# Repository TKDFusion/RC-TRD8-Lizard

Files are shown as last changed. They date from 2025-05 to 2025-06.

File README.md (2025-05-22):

Lizard is a 3D printed RC race car for onroad usage. The full description of this project is available on Instructables: https://www.instructables.com/Lizard-3D-Printed-RC-Race-Car/

Here, you can find the Gerber files for the PCBs and the sketches required for the ESP32 microcontroller in the remote control and in the car. Also, you can find the codes required to operate a separate data logger alongside the car, including MATLAB functions to evaluate the recorded data graphically. Further, all files for printing are provided as .stl and .stp files.

Also, I added the BOM as an Excel file, and you can find .stp files of the different part groups as well as of the full car assembly, as an aid in assembling the car.

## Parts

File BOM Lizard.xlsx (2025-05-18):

Group | Part | Content | Quantity | Description/comment | Source/Link | Price per unit | Total | Sum
Actuators | Cytron MD 20A | 1 | 1 | 20 A brushed DC motor driver | https://eu.robotshop.com/de/products/cytron-20a-6-30v-dc-motorsteuerung | 23.80 € | 23.80 € | 954.12 €
Actuators | 775 12 V 10k rpm 150 W | 1 | 1 | 775 brushed DC motor | https://www.amazon.de/dp/B07BGWMYYM | 13.99 € | 13.99 €
Actuators | 40-45mm motor cooler | 1 | 1 | Cooling block for DC motor | https://www.ebay.de/itm/224586911069 | 15.95 € | 15.95 €
Actuators | Claw clutch (5 mm shaft coupler) | 1 | 1 | shaft adapter for 775 motor | https://www.amazon.de/dp/B09MLV2G45/ | 10.99 € | 10.99 €
Actuators | Servo motor | 1 | 1 | Graupner DES 708 BB MG | https://www.derkum-modellbau.com/rc-_-elektronik/servos/servos/graupner-des-708-bb-mg-digital-servo | 43.90 € | 43.90 €
Actuators | Servo saver | 1 | 1 | Tamiya high torque servo saver | https://tamico.de/Tamiya-Servo-Saver-Hi-Torque-weiss-50473 | 13.39 € | 13.39 €
Wheels | Carson 1:8 buggy | 2 | 2 | Carson buggy wheels | https://www.amazon.de/Carson-500900075-Felgen-Set-Modellbauzubeh%C3%B6r-schwarz/dp/B003MX6LOG/ | 11.99 € | 23.98 €
Batteries | SLS XTRON 5000MAH 3S1P | 1 | 1 | car battery | https://www.stefansliposhop.de/akkus/sls-xtron/sls-xtron-20c/sls-xtron-5000mah-3s1p-11-1v-20c-40c::985.html | 51.90 € | 51.90 €
Batteries | Duracell NiMH AA 2500 mAh | 4 | 2 | RC batteries | https://www.reichelt.de/nimh-akku-aa-mignon-2500-mah-4er-pack-dura-nimh-aa4-p357195.html | 12.95 € | 25.90 €
Bearings | 683ZZ | 20 | 2 | 3x7x3 | https://www.amazon.de/sourcing-map-Rillenkugellager-Doppelschild-Kohlenstoffstahl/dp/B07H5HXND9/ | 9.49 € | 18.98 €
Bearings | 6802ZZ | 10 | 2 | 15x24x5 | https://www.amazon.de/XiKe-Kugellager-15x24x5mm-Abgedichtet-Rillenkugellager/dp/B09SD74PZV/ | 11.59 € | 23.18 €
Bearings | 6804ZZ | 10 | 1 | 20x32x7 | https://www.amazon.de/XiKe-Kugellager-20x32x7mm-Abgedichtet-Rillenkugellager/dp/B09SD8RKJT/ | 12.99 € | 12.99 €
Bearings | 608ZZ | 20 | 1 | 8x22x7 | https://www.amazon.de/HonLena-Kugellager-Shielded-Rillenkugellager-Skateboard/dp/B08K936Y1Z/ | 9.99 € | 9.99 €
Bearings | 605ZZ | 10 | 1 | 5x14x5 | https://www.amazon.de/sourcing-map-Rillenkugellager-5mmx14mmx5mm-Kohlenstoffstahl/dp/B07H936D3C/ | 7.99 € | 7.99 €
Bearings | MR85ZZ | 10 | 1 | 5x8x2.5 | https://www.amazon.de/dp/B07CKN7NPK | 8.14 € | 8.14 €
Bearings | 0303 sleeve bearing | 50 | 1 | 3x4.5x3 | https://www.amazon.de/dp/B06Y6D951G | 8.63 € | 8.63 €
Bearings | 0306 sleeve bearing | 50 | 1 | 3x4.5x6 | https://www.amazon.de/dp/B06Y617JGS | 9.66 € | 9.66 €
Connectors | Molex 16-02-0102 | 100 | 1 | Molex SL female crimp pin | https://www.mouser.de/ProductDetail/Molex/16-02-0102?qs=UAyrm%2FnZ%252BCifWkt7bqgfPw%3D%3D | 8.50 € | 8.50 €
Connectors | Molex 70543-0001 | 10 | 1 | Molex SL 2-pin socket | https://www.mouser.de/ProductDetail/Molex/70543-0001?qs=tYx%252BZc2nXqpCsE0XoulATg%3D%3D | 7.60 € | 7.60 €
Connectors | Molex 70543-0002 | 10 | 1 | Molex SL 3-pin socket | https://www.mouser.de/ProductDetail/Molex/70543-0002?qs=tYx%252BZc2nXqrtKxtMAO73sw%3D%3D | 7.67 € | 7.67 €
Connectors | Molex 70543-0003 | 10 | 1 | Molex SL 4-pin socket | https://www.mouser.de/ProductDetail/Molex/70543-0003?qs=tYx%252BZc2nXqp%2Fu7bSTX42XQ%3D%3D | 8.59 € | 8.59 €
Connectors | Molex 50-57-9402 | 10 | 1 | Molex SL 2-pin female connector | https://www.mouser.de/ProductDetail/Molex/50-57-9402?qs=u6Gr9%2FNt%252B%2F9jh%2FRowNBxRQ%3D%3D | 2.53 € | 2.53 €
Connectors | Molex 50-57-9403 | 10 | 1 | Molex SL 3-pin female connector | https://www.mouser.de/ProductDetail/Molex/50-57-9403?qs=u6Gr9%2FNt%252B%2F9Ok3bHhq8UPA%3D%3D | 1.71 € | 1.71 €
Connectors | Molex 50-57-9404 | 10 | 1 | Molex SL 4-pin female connector | https://www.mouser.de/ProductDetail/Molex/50-57-9404?qs=u6Gr9%2FNt%252B%2F%2FUw3Dr7T8xxg%3D%3D | 2.17 € | 2.17 €
Connectors | Jamara XT60 | 1 | 1 | M/F pair of high-current connectors | https://www.reichelt.de/steckverbinder-fuer-li-polymer-akkus-2-polig-xt60-hstxt60-stbu-p207648.html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 | 1.99 € | 1.99 €
Electronics | ESP32 MCU | 2 | 1 | with connector for external antenna | https://www.amazon.de/iHaospace-ESP32-WROOM-32U-ESP32-DevKitC-Development-Entwicklungsboard/dp/B0CT3BHJ4C/ | 15.99 € | 15.99 €
Electronics | Antenna | 2 | 1 | external antenna for ESP32 | https://www.amazon.de/2-4GHz-Omnidirektionale-Antenne-802-11n-Pigtail/dp/B07FDN82D8/ | 6.99 € | 6.99 €
Electronics | ADS1115 | 1 | 2 | ADC boards | https://www.amazon.de/AZDelivery-ADS1115-Kanäle-Arduino-Raspberry/dp/B07QHWLTTS/ | 5.99 € | 11.98 €
Electronics | Marquardt 01801.1148-02 | 1 | 2 | Marquardt on-off switch, series 1801 | https://www.reichelt.de/de/de/shop/produkt/wippschalter_ein_-_aus_1_polig_schwarz-257132 | 1.60 € | 3.20 €
Electronics | ONPOW anti-vandal push button | 1 | 4 | with LED, 16 mm mounting hole | https://www.pollin.de/p/onpow-vandalismusgeschuetzter-taster-220-v-ac-0-5-a-1no-weiss-421220 | 4.55 € | 18.20 €
Electronics | Battery holder | 1 | 1 | 6xAA | https://funduinoshop.com/diy-werkstatt/stromversorgung/batteriefaecher-und-klemmen/batteriefach-6x-aa-9v-ohne-stecker | 1.97 € | 1.97 €
Electronics | Omeg PC20BU 10k linear | 1 | 1 | Poti with 6 mm shaft | https://www.pollin.de/p/omeg-potentiometer-pc20bu-10-ko-linear-240663 | 1.90 € | 1.90 €
Electronics | Bourns 93R1AR2215L | 1 | 2 | High-quality poti with 6 mm shaft | https://www.reichelt.de/drehpotentiometer-10-kohm-linear-6-mm-bou-93r1ar22a15l-p232657.html | 6.25 € | 12.50 €
Electronics | Sunon MF50151VX-1000U-A99 | 1 | 2 | 50x50x15 mm 12 V axial fan | https://www.reichelt.de/de/de/shop/produkt/luefter_12_vdc_50x50x15mm_serie_me-397682 | 2.99 € | 5.98 €
Electronics | 0.96" OLED display | 1 | 2 | 128x64 px, SSD1306 chip | https://www.amazon.de/AZDelivery-Display-Arduino-Raspberry-gratis/dp/B01L9GC470 | 6.62 € | 13.24 €
Electronics | NTC temp sensor | 1 | 2 | 10k, B-value 3435 | https://www.amazon.de/InLine-Temperatursensor-mit-Kabel-1m/dp/B001IQ0L2M | 8.48 € | 16.96 €
Electronics | Speed sensor | 1 | 1 | HC-020K wheel encoder | https://funduinoshop.com/elektronische-module/elektromotoren-und-zubehoer/servomotoren/hc-020k-schrittzaehler-fuer-motoren-wheel-encoder | 2.57 € | 2.57 €
Electronics | LED stripe red | 1 | 1 | 480 LEDs/m, 4 mm width, 2 m length | https://www.amazon.de/COB-LED-Fosingut-USB-Hintergrundbeleuchtung/dp/B0D3T8R8HF | 10.99 € | 10.99 €
Electronics | LED flashlight | 2 | 1 | designed for 2xAAA battery | https://www.amazon.de/flintronic-Taschenlampe-Wasserdicht-AAA-Batterien-enthalten/dp/B09MM7L6LG | 7.99 € | 7.99 €
Filament | PETG filament | 1 kg | 2 | Prusament Jet Black | https://www.prusa3d.com/product/prusament-petg-jet-black-1kg/ | 29.99 € | 59.98 €
Filament | PETG filament | 1 kg | 1 | Prusament Jungle Green | https://www.prusa3d.com/product/prusament-petg-jungle-green-1kg/ | 29.99 € | 29.99 €
Filament | TPU filament | 750 g | 1 | BASF TPU64D | https://www.galaxus.de/de/s1/product/basf-tpu64d-schwarz-175-mm-750-g-tpu-175-mm-750-g-schwarz-3d-filament-18455255 | 48.94 € | 48.94 €
Magnets | Neodymium disc magnet (south) | 1 | 4 | 8x3.5x3 | https://www.magnethandel.de/neodym-ringmagnete-senkung-sued-8-35-3-mm-schwarz | 0.31 € | 1.24 €
Magnets | Neodymium disc magnet (north) | 1 | 4 | 8x3.5x3 | https://www.magnethandel.de/neodym-ringmagnete-senkung-nord-8-35-3-mm-schwarz | 0.31 € | 1.24 €
Metal bars | Steel round bar | 1 m | 1 | 3 mm diameter (not more than 3 mm!) | local hardware store | 5.00 € | 5.00 €
Metal bars | Steel round bar | 1 m | 1 | 4 mm diameter | local hardware store | 5.00 € | 5.00 €
PCB parts | Gaptec LC78_05-2.0 | 1 | 1 | 5V 2A DC-DC converter | https://www.reichelt.de/dc-dc-wandler-6-5-30-vin-5-0-vout-2-a-sip-3-lc78-05-2-0-p242830.html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 | 13.30 € | 13.30 €
PCB parts | Traco TSR 1-2433E | 1 | 1 | 3V3 1A DC-DC converter | https://www.reichelt.de/de/de/shop/produkt/dc_dc-wandler_tsr_1e_1_a_6-36_3_3_vdc_sil-3-288646?search=2433e | 3.99 € | 3.99 €
PCB parts | Gaptec LC78_03-2.0 | 1 | 1 | 3V3 2A DC-DC converter | https://www.reichelt.de/de/de/shop/produkt/dc_dc-wandler_4_5_-_30_vin_3_3_vout_2_a_sip-3-242828 | 13.30 € | 13.30 €
PCB parts | Quadrios resistor set | 1 | 1 | 20x20 different resistors | https://www.pollin.de/p/quadrios-widerstands-set-201711p004-metallschicht-0-5-watt-1-800557 | 12.90 € | 12.90 €
PCB parts | Panasonic FC 100/50 | 1 | 2 | Radial Cap, 100 µF, 50 V, 5 mm spacing | https://www.reichelt.de/elko-radial-100-f-50-v-105-c-low-esr-10-x-12-5-mm-rm-5-0-rad-fc-100-50-p84620.html | 0.22 € | 0.44 €
PCB parts | ECC KTS500B106K (X7R) | 1 | 2 | SMD Capacitor, 10 µF, 50 V, G2220 | https://www.reichelt.de/smd-kerko-2220-10-f-50-v-10-mlcc-ecc-kts500b106k-p256486.html | 0.99 € | 1.98 €
PCB parts | X7R-G1206 22/10 | 1 | 6 | SMD Capacitor, 22 µF, 10 V, G1206 | https://www.reichelt.de/smd-vielschichtkondensator-g1206-22-f-10v-x7r-g1206-22-10-p89742.html | 0.26 € | 1.56 €
PCB parts | WAL 0805B104K500 | 1 | 3 | SMD Capacitor, 100 nF, 50 V, 0805(2012) | https://www.reichelt.de/smd-kerko-0805-100-nf-50v-10-x7r-mlcc-wal-0805b104k500-p346808.html | 0.03 € | 0.09 €
PCB parts | WAL 0805B102K500 | 1 | 1 | SMD Capacitor, 1 nF, 50 V | https://www.reichelt.de/de/de/shop/produkt/smd-kerko_0805_1_nf_50v_10_x7r_mlcc-346784 | 0.03 € | 0.03 €
PCB parts | X5R-G0805 10/16 | 1 | 1 | SMD Capacitor, 10 µF, 16 V (0805) | https://www.reichelt.de/de/de/shop/produkt/smd-vielschichtkondensator_g0805_-_10_f_16v-89734 | 0.05 € | 0.05 €
PCB parts | ACS712 ELCTR-30 | 1 | 1 | SOIC-8 current sensor | https://www.reichelt.de/de/de/shop/produkt/stromsensor_ac_dc_5_v_soic-8-237785 | 3.20 € | 3.20 €
PCB parts | IRLML 6244 | 1 | 4 | SMD MOSFET | https://www.reichelt.de/de/de/shop/produkt/mosfet_n-ch_20v_6_3a_0_021r_sot-23-132145 | 0.15 € | 0.60 €
PCB parts | WAGO 2604-3104 | 1 | 1 | PCB terminal block | https://www.reichelt.de/de/de/shop/produkt/leiterplattenklemme_-_rm_5_mm_4_mm_4-polig-195366 | 3.50 € | 3.50 €
PCB parts | 20-pin socket terminal strip | 1 | 4 | 2.54 mm spacing, height 8.5 mm | https://www.reichelt.de/20pol-buchsenleiste-gerade-rm-2-54-h-8-5mm-bl-1x20g8-2-54-p51827.html | 0.30 € | 1.20 €
PCB parts | 10-pin socket terminal strip | 1 | 2 | 2.54 mm spacing, height 8.5 mm | https://www.reichelt.de/10pol-buchsenleiste-gerade-rm-2-54-h-8-5mm-bl-1x10g8-2-54-p51826.html | 0.22 € | 0.44 €
PCB parts | IMAXX H7810 | 1 | 1 | miniOTO fuse holder | https://www.reichelt.de/kfz-sicherungshalter-minioto-30-a-125-v-printmontage-imaxx-h7810-p229120.html | 0.99 € | 0.99 €
PCB parts | IMAXX F7030 | 1 | 1 | miniOTO fuse, 30 A | https://www.reichelt.de/kfz-sicherung-minioto-30-a-gruen-imaxx-f7030-p242101.html | 0.33 € | 0.33 €
PCB parts | IRLZ 44N | 1 | 3 | n-Channel logic level MOSFET, TO-220 | https://www.reichelt.de/mosfet-n-ch-55v-47a-110w-to-220ab-irlz-44n-p129819.html | 0.70 € | 2.10 €
PCB parts | IRFP7430PBF | 1 | 1 | n-Channel power MOSFET, TO-247 | https://www.reichelt.de/mosfet-n-kanal-40-v-195-a-rds-on-0-001-ohm-to247ac-irfp7430pbf-p257333.html | 3.10 € | 3.10 €
PCB parts | 1N-5819 | 1 | 1 | Diode | https://www.reichelt.de/de/de/shop/produkt/schottkydiode_40_v_1_a_do-41-41850 | 0.05 € | 0.05 €
PCB parts | PCA9685 | 1 | 1 | TSSOP-28 IC, PWM driver | https://www.conrad.de/de/p/nxp-semiconductors-pca9685pw-112-pmic-led-treiber-linear-tssop-28-oberflaechenmontage-1116598.html | 3.49 € | 3.49 €
PCBs | Manufacturing of car PCB | 3 | 1 | Gerber files on GitHub | https://aisler.net/ | 30.19 € | 30.19 €
PCBs | Manufacturing of RC PCB | 3 | 1 | Gerber files on GitHub | https://aisler.net/ | 22.98 € | 22.98 €
Screws & nuts | M3x6 | 100 | 1 | cylinder head (18 needed) | https://shop.der-schraubenladen.de/DIN-912-ISO-4762-Zylinderschraube-Innensechskant-Edelstahl-A2/SW11250.69 | 3.82 € | 3.82 €
Screws & nuts | M3x8 | 100 | 2 | cylinder head (153 needed) | https://shop.der-schraubenladen.de/DIN-912-ISO-4762-Zylinderschraube-Innensechskant-Edelstahl-A2/SW11250.70 | 3.58 € | 7.16 €
Screws & nuts | M3x10 | 100 | 1 | cylinder head (56 needed) | https://shop.der-schraubenladen.de/DIN-912-ISO-4762-Zylinderschraube-Innensechskant-Edelstahl-A2/SW11250.71 | 3.58 € | 3.58 €
Screws & nuts | M3x12 | 100 | 1 | cylinder head (45 needed) | https://shop.der-schraubenladen.de/DIN-912-ISO-4762-Zylinderschraube-Innensechskant-Edelstahl-A2/SW11250.72 | 3.90 € | 3.90 €
Screws & nuts | M3x16 | 100 | 1 | cylinder head (38 needed) | https://shop.der-schraubenladen.de/DIN-912-ISO-4762-Zylinderschraube-Innensechskant-Edelstahl-A2/SW11250.74 | 4.37 € | 4.37 €
Screws & nuts | M3x20 | 100 | 1 | cylinder head (25 needed) | https://shop.der-schraubenladen.de/DIN-912-ISO-4762-Zylinderschraube-Innensechskant-Edelstahl-A2/SW11250.76 | 5.54 € | 5.54 €
Screws & nuts | M3x22 | 100 | 1 | cylinder head (24 needed) | https://shop.der-schraubenladen.de/DIN-912-ISO-4762-Zylinderschraube-Innensechskant-Edelstahl-A2/SW11250.77 | 6.00 € | 6.00 €
Screws & nuts | M3x25 | 100 | 1 | cylinder head, fully threaded (20 needed) | https://shop.der-schraubenladen.de/DIN-912-ISO-4762-Zylinderschraube-Innensechskant-Vollgewinde-Edelstahl-A2/SW11251M | 20.60 € | 20.60 €
Screws & nuts | M3x30 | 100 | 1 | cylinder head (9 needed) | https://shop.der-schraubenladen.de/DIN-912-ISO-4762-Zylinderschraube-Innensechskant-Edelstahl-A2/SW11250.79 | 7.57 € | 7.57 €
Screws & nuts | M3x35 | 100 | 1 | cylinder head (4 needed) | https://shop.der-schraubenladen.de/DIN-912-ISO-4762-Zylinderschraube-Innensechskant-Edelstahl-A2/SW11250.80 | 8.66 € | 8.66 €
Screws & nuts | M3x50 | 100 | 1 | cylinder head (2 needed) | https://shop.der-schraubenladen.de/DIN-912-ISO-4762-Zylinderschraube-Innensechskant-Edelstahl-A2/SW11250.83 | 11.70 € | 11.70 €
Screws & nuts | M3 nut | 100 | 2 | 198 needed | https://shop.der-schraubenladen.de/DIN-439-ISO-4035-Sechskantmutter-Edelstahl-A2/SW12301.11 | 3.90 € | 7.80 €
Screws & nuts | M3 washer | 100 | 1 |  | https://shop.der-schraubenladen.de/DIN-125-A-ISO-7089-Unterlegscheibe-Edelstahl-A2/SW11409.25 | 2.95 € | 2.95 €
Screws & nuts | M3 locknut | 100 | 1 | 48 needed | https://shop.der-schraubenladen.de/DIN-985-ISO-10511-Sechskantmutter-Edelstahl-A2-selbstsichernd-niedrige-Form/SW10918.5 | 2.95 € | 2.95 €
Screws & nuts | M3 threaded insert | 100 | 2 | 157 needed | https://www.ruthex.de/collections/gewindeeinsatze/products/ruthex-gewindeeinsatz-m3-100-stuck-rx-m3x5-7-messing-gewindebuchsen | 8.99 € | 17.98 €
Screws & nuts | M3x10 | 100 | 1 | countersunk | https://www.amazon.de/dp/B07YZMB95S/ref=pe_27091401_487027711_TE_SCE_dp_1 | 7.21 € | 7.21 €
Screws & nuts | M4x8 | 100 | 1 | cylinder head (2 needed) | https://shop.der-schraubenladen.de/DIN-912-ISO-4762-Zylinderschraube-Innensechskant-Edelstahl-A2/SW11250.91 | 4.83 € | 4.83 €
Springs | 0X-DF1720 | 1 | 4 | For rear shock absorbers | https://www.febrotec.de/de-DE/druckfedern/schraubendruckfedern/0x-df1720/ | 2.79 € | 11.16 €
Springs | 0X-DF1709 | 1 | 2 | For front shock absorbers | https://www.febrotec.de/de-DE/druckfedern/schraubendruckfedern/0x-df1709/ | 2.79 € | 5.58 €
Springs | 7x19 mm spring | 30 | 1 | Box with various sizes | https://www.amazon.de/Kraftmann-9806-Federn-Sortiment-Druckfedern-Sortimentskasten/dp/B07WFPPXXX/ | 7.28 € | 7.28 €
Wires | 0.25mm² stranded wire | 100 m | 1 | black | https://www.pollin.de/p/rautronic-litze-1x0-25-100m-spule-schwarz-liyv-563441 | 16.70 € | 16.70 €
Wires | 2.5mm² stranded wire | 10 m | 1 | black | https://www.pollin.de/p/rautronic-silikon-litze-2-5-mm2-schwarz-10-m-563314 | 10.50 € | 10.50 €
Wires | 2.5 mm² stranded wire | 10 m | 1 | red | https://www.pollin.de/p/rautronic-silikon-litze-2-5-mm2-rot-10-m-563313 | 10.50 € | 10.50 €

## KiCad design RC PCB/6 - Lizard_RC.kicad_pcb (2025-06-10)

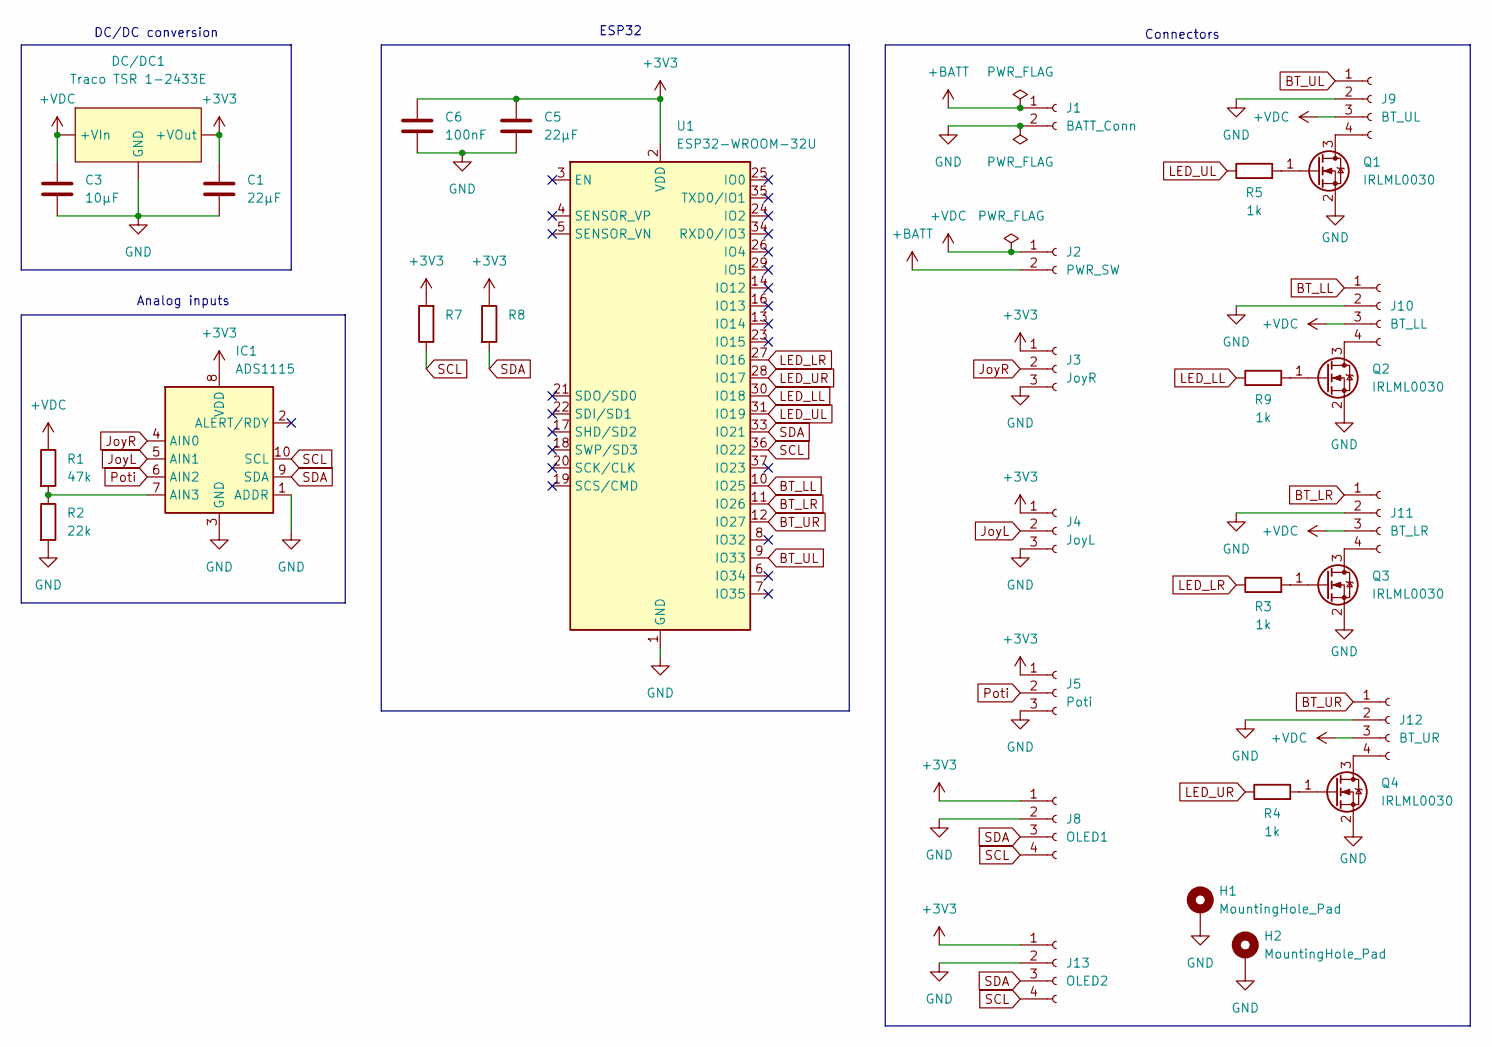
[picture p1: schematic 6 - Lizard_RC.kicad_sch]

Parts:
C1, C5: 22µF; C_1206_3216Metric_Pad1.33x1.80mm_HandSolder
C3: 10µF; C_2220_5750Metric_Pad1.97x5.40mm_HandSolder
C6: 100nF; C_0805_2012Metric_Pad1.18x1.45mm_HandSolder
DC/DC1: Traco TSR 1-2433E; LME78_03-1.0
H1, H2: MountingHole_Pad; MountingHole_3.5mm_Pad_TopBottom
IC1: ADS1115
J1: BATT_Conn; Molex_SL_171971-0002_1x02_P2.54mm_Vertical
J2: PWR_SW; Molex_SL_171971-0002_1x02_P2.54mm_Vertical
J3: JoyR; Molex_SL_171971-0003_1x03_P2.54mm_Vertical
J4: JoyL; Molex_SL_171971-0003_1x03_P2.54mm_Vertical
J5: Poti; Molex_SL_171971-0003_1x03_P2.54mm_Vertical
J8: OLED1; Molex_SL_171971-0004_1x04_P2.54mm_Vertical
J9: BT_UL; Molex_SL_171971-0004_1x04_P2.54mm_Vertical
J10: BT_LL; Molex_SL_171971-0004_1x04_P2.54mm_Vertical
J11: BT_LR; Molex_SL_171971-0004_1x04_P2.54mm_Vertical
J12: BT_UR; Molex_SL_171971-0004_1x04_P2.54mm_Vertical
J13: OLED2; Molex_SL_171971-0004_1x04_P2.54mm_Vertical
Q1, Q2, Q3, Q4: IRLML0030; SOT-23_Handsoldering
R1: 47k; R_Axial_DIN0309_L9.0mm_D3.2mm_P12.70mm_Horizontal
R2: 22k; R_Axial_DIN0309_L9.0mm_D3.2mm_P12.70mm_Horizontal
R3, R4, R5, R9: 1k; R_Axial_DIN0309_L9.0mm_D3.2mm_P12.70mm_Horizontal
R7, R8: R_Axial_DIN0309_L9.0mm_D3.2mm_P12.70mm_Horizontal
U1: ESP32-WROOM-32U; NodeMCU-ESP32

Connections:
+3V3: C1.1, C5.1, C6.1, DC/DC1.3 (+VOut), IC1.8 (VDD), J3.1, J4.1, J5.1, J8.1, J13.1, R7.2, R8.1, U1.2 (VDD)
+BATT: J1.1, J2.2
+VDC: C3.1, DC/DC1.1 (+VIn), J2.1, J9.3, J10.3, J11.3, J12.3, R1.1
BT_LL: J10.1, U1.10 (IO25)
BT_LR: J11.1, U1.11 (IO26)
BT_UL: J9.1, U1.9 (IO33)
BT_UR: J12.1, U1.12 (IO27)
GND: C1.2, C3.2, C5.2, C6.2, DC/DC1.2 (GND), H1.1, H2.1, IC1.1 (ADDR), IC1.3 (GND), J1.2, J3.3, J4.3, J5.3, J8.2, J9.2, J10.2, J11.2, J12.2, J13.2, Q1.2 (S), Q2.2 (S), Q3.2 (S), Q4.2 (S), R2.2, U1.1 (GND), U1.15 (GND), U1.38 (GND)
JoyL: IC1.5 (AIN1), J4.2
JoyR: IC1.4 (AIN0), J3.2
LED_LL: R9.1, U1.30 (IO18)
LED_LR: R3.1, U1.27 (IO16)
LED_UL: R5.1, U1.31 (IO19)
LED_UR: R4.1, U1.28 (IO17)
unnamed: IC1.7 (AIN3), R1.2, R2.1
unnamed: J9.4, Q1.3 (D)
unnamed: J10.4, Q2.3 (D)
unnamed: J11.4, Q3.3 (D)
unnamed: J12.4, Q4.3 (D)
unnamed: Q1.1 (G), R5.2
unnamed: Q2.1 (G), R9.2
unnamed: Q3.1 (G), R3.2
unnamed: Q4.1 (G), R4.2
Poti: IC1.6 (AIN2), J5.2
SCL: IC1.10 (SCL), J8.4, J13.4, R7.1, U1.36 (IO22)
SDA: IC1.9 (SDA), J8.3, J13.3, R8.2, U1.33 (IO21)

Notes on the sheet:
DC/DC conversion
ESP32
Connectors
Analog inputs

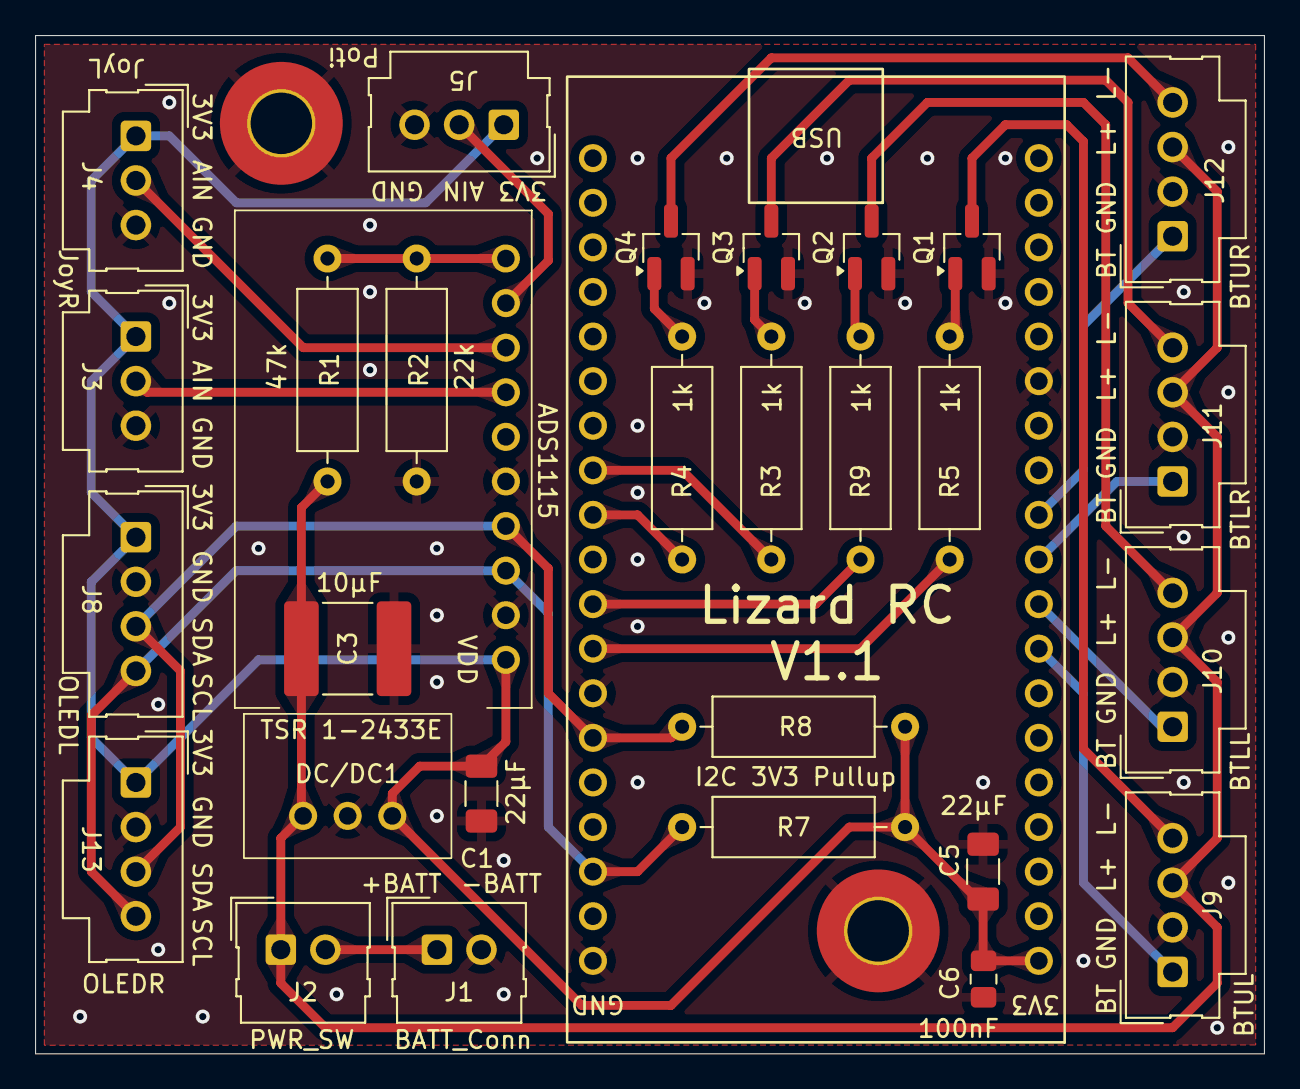
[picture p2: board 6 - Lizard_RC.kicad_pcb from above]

Board: 2 copper layers, 70.0 x 58.0 mm, 32 parts (0 on the bottom side), 26 nets.

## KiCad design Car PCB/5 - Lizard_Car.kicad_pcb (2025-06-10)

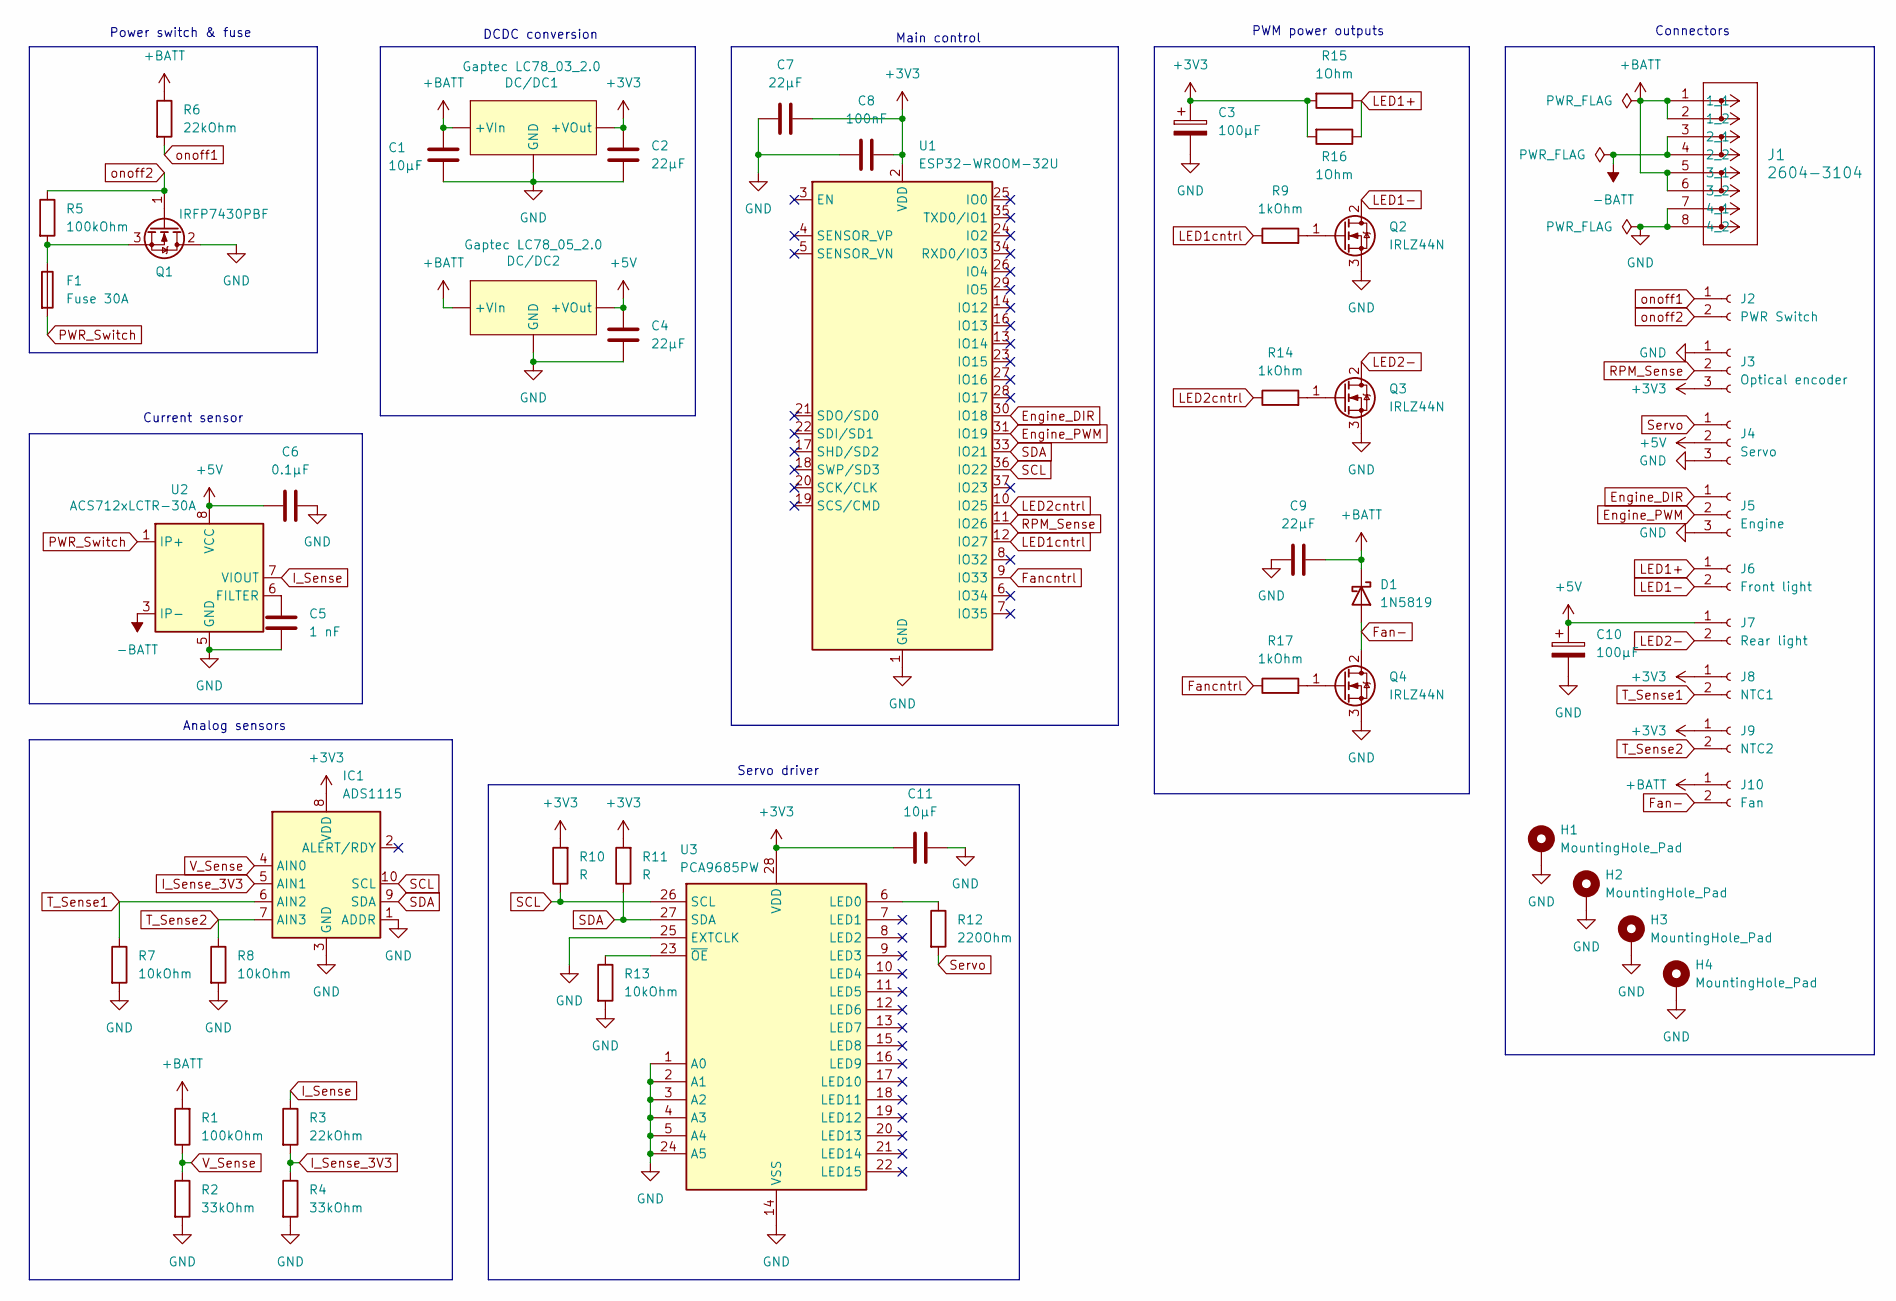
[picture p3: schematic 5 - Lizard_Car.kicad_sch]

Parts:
C1: 10µF; C_2220_5750Metric_Pad1.97x5.40mm_HandSolder
C2, C4, C7, C9: 22µF; C_1206_3216Metric_Pad1.33x1.80mm_HandSolder
C3, C10: 100µF; CP_Radial_D10.0mm_P5.00mm
C5: 1 nF; C_0805_2012Metric_Pad1.18x1.45mm_HandSolder
C6: 0.1µF; C_0805_2012Metric_Pad1.18x1.45mm_HandSolder
C8: 100nF; C_0805_2012Metric_Pad1.18x1.45mm_HandSolder
C11: 10µF; C_0805_2012Metric_Pad1.18x1.45mm_HandSolder
D1: 1N5819; D_DO-41_SOD81_P10.16mm_Horizontal
DC/DC1: Gaptec LC78_03_2.0; LC78_05_2.0
DC/DC2: Gaptec LC78_05_2.0; LC78_05_2.0
F1: Fuse 30A; iMAXX_H7810
H1, H2, H3, H4: MountingHole_Pad; MountingHole_3.2mm_M3_Pad_TopBottom
IC1: ADS1115
J1: 2604-3104; CONN4_2604-3104_WAG
J2: PWR Switch; Molex_SL_171971-0002_1x02_P2.54mm_Vertical
J3: Optical encoder; Molex_SL_171971-0003_1x03_P2.54mm_Vertical
J4: Servo; Molex_SL_171971-0003_1x03_P2.54mm_Vertical
J5: Engine; Molex_SL_171971-0003_1x03_P2.54mm_Vertical
J6: Front light; Molex_SL_171971-0002_1x02_P2.54mm_Vertical
J7: Rear light; Molex_SL_171971-0002_1x02_P2.54mm_Vertical
J8: NTC1; Molex_SL_171971-0002_1x02_P2.54mm_Vertical
J9: NTC2; Molex_SL_171971-0002_1x02_P2.54mm_Vertical
J10: Fan; Molex_SL_171971-0002_1x02_P2.54mm_Vertical
Q1: IRFP7430PBF; TO247 vertical MOSFET
Q2, Q3, Q4: IRLZ44N; TO-220-3_Vertical
R1, R5: 100kOhm; R_Axial_DIN0309_L9.0mm_D3.2mm_P2.54mm_Vertical
R2, R4: 33kOhm; R_Axial_DIN0309_L9.0mm_D3.2mm_P2.54mm_Vertical
R3, R6: 22kOhm; R_Axial_DIN0309_L9.0mm_D3.2mm_P2.54mm_Vertical
R7, R8: 10kOhm; R_Axial_DIN0309_L9.0mm_D3.2mm_P12.70mm_Horizontal
R9, R14, R17: 1kOhm; R_Axial_DIN0309_L9.0mm_D3.2mm_P2.54mm_Vertical
R10, R11: R; R_Axial_DIN0309_L9.0mm_D3.2mm_P2.54mm_Vertical
R12: 220Ohm; R_Axial_DIN0309_L9.0mm_D3.2mm_P12.70mm_Horizontal
R13: 10kOhm; R_Axial_DIN0309_L9.0mm_D3.2mm_P2.54mm_Vertical
R15, R16: 1Ohm; R_Axial_DIN0309_L9.0mm_D3.2mm_P2.54mm_Vertical
U1: ESP32-WROOM-32U; NodeMCU-ESP32
U2: ACS712xLCTR-30A; SOIC-8_3.9x4.9mm_P1.27mm
U3: PCA9685PW; TSSOP-28_4.4x9.7mm_P0.65mm

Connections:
+3V3: C2.1, C3.1, C7.1, C8.1, C11.1, DC/DC1.3 (+VOut), IC1.8 (VDD), J3.3, J8.1, J9.1, R10.2, R11.2, R15.2, R16.2, U1.2 (VDD), U3.28 (VDD)
+5V: C4.1, C6.2, C10.1, DC/DC2.3 (+VOut), J4.2, J7.1, U2.8 (VCC)
+BATT: C1.1, C9.1, D1.1 (K), DC/DC1.1 (+VIn), DC/DC2.1 (+VIn), J1.1 (1_1), J1.2 (1_2), J1.5 (3_1), J1.6 (3_2), J10.1, R1.2, R6.1
-BATT: J1.3 (2_1), J1.4 (2_2), U2.3 (IP-), U2.4 (IP-)
Engine_DIR: J5.1, U1.30 (IO18)
Engine_PWM: J5.2, U1.31 (IO19)
Fan-: D1.2 (A), J10.2, Q4.2 (D)
Fancntrl: R17.1, U1.9 (IO33)
GND: C1.2, C2.2, C3.2, C4.2, C5.2, C6.1, C7.2, C8.2, C9.2, C10.2, C11.2, DC/DC1.2 (GND), DC/DC2.2 (GND), H1.1, H2.1, H3.1, H4.1, IC1.1 (ADDR), IC1.3 (GND), J1.7 (4_1), J1.8 (4_2), J3.1, J4.3, J5.3, Q1.2 (D), Q2.3 (S), Q3.3 (S), Q4.3 (S), R2.2, R4.2, R7.2, R8.2, R13.2, U1.1 (GND), U1.15 (GND), U1.38 (GND), U2.5 (GND), U3.1 (A0), U3.2 (A1), U3.3 (A2), U3.4 (A3), U3.5 (A4), U3.14 (VSS), U3.24 (A5), U3.25 (EXTCLK)
I_Sense: R3.1, U2.7 (VIOUT)
I_Sense_3V3: IC1.5 (AIN1), R3.2, R4.1
LED1+: J6.1, R15.1, R16.1
LED1-: J6.2, Q2.2 (D)
LED1cntrl: R9.1, U1.12 (IO27)
LED2-: J7.2, Q3.2 (D)
LED2cntrl: R14.1, U1.10 (IO25)
unnamed: F1.1, Q1.3 (S), R5.2
unnamed: Q2.1 (G), R9.2
unnamed: Q3.1 (G), R14.2
unnamed: Q4.1 (G), R17.2
unnamed: C5.1, U2.6 (FILTER)
unnamed: R12.1, U3.6 (LED0)
unnamed: R13.1, U3.23 (~OE)
PWR_Switch: F1.2, U2.1 (IP+), U2.2 (IP+)
RPM_Sense: J3.2, U1.11 (IO26)
SCL: IC1.10 (SCL), R10.1, U1.36 (IO22), U3.26 (SCL)
SDA: IC1.9 (SDA), R11.1, U1.33 (IO21), U3.27 (SDA)
Servo: J4.1, R12.2
T_Sense1: IC1.6 (AIN2), J8.2, R7.1
T_Sense2: IC1.7 (AIN3), J9.2, R8.1
V_Sense: IC1.4 (AIN0), R1.1, R2.1
onoff1: J2.1, R6.2
onoff2: J2.2, Q1.1 (G), R5.1

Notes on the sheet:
Current sensor
Connectors
PWM power outputs
Servo driver
Analog sensors
DCDC conversion
Power switch & fuse
Main control

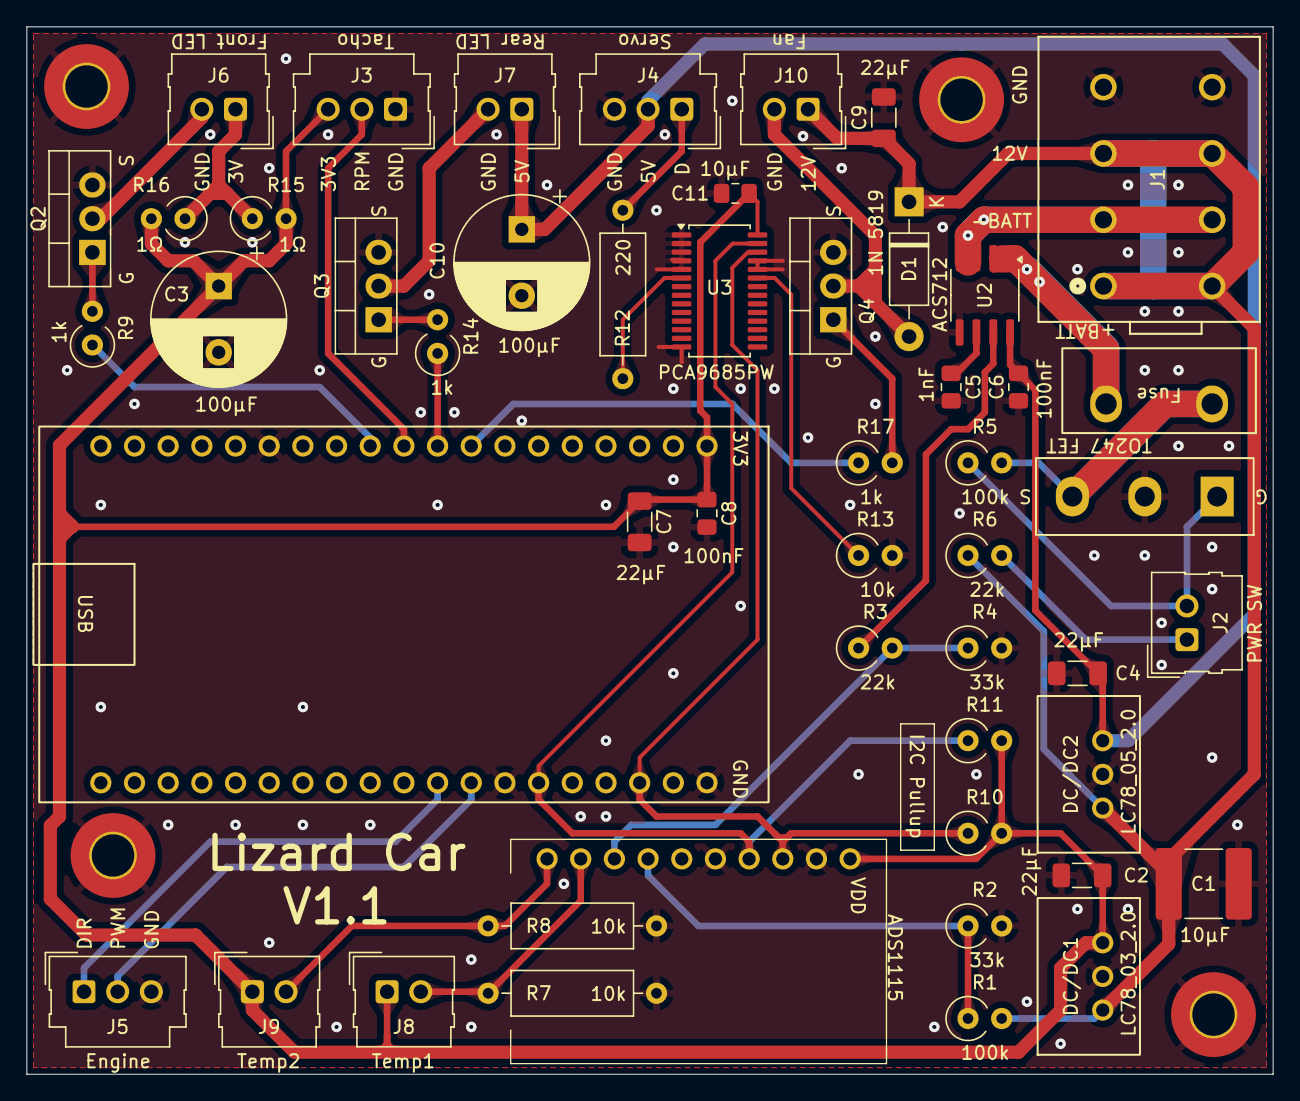
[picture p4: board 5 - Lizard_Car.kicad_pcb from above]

Board: 2 copper layers, 94.0 x 79.0 mm, 54 parts (0 on the bottom side), 33 nets.

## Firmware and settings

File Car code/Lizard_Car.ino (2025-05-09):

/*
  This code is developed for Lizard, an open source RC car. This code runs on the car's mircrontroller.
  The code was designed in Arduino IDE for an ESP32 microcontroller (ESP32-WROOM-32U; 38 pin version of NodeMCU developer board)
*/

/*
  IMPORTANT: This code is written for esp32 boards manager version 2 (tested successfully with esp32 2.0.17).
  It does not work with 3.x.x versions of Espressif Systems' esp32 boards managers (see also https://docs.espressif.com/projects/arduino-esp32/en/latest/migration_guides/2.x_to_3.0.html).
*/

//Required libraries
#include <Wire.h> //library for I2C devices
#include <Adafruit_ADS1X15.h> //library for ADS1115 ADC
#include <Adafruit_PWMServoDriver.h> //library for PCA9685 servo driver
#include <WiFi.h> //library for wireless communication
#include <esp_now.h> //library for bidirectional wireless communication between two ESP32
#include <esp_wifi.h> //needed to adjust the MAC address
#include <Preferences.h> //library for storing variables in flash memory

//Pin definitions
#define dir 18 //main motor direction
#define pwm 19 //main motor pwm input
#define rear 25 //tail light
#define front 27 //front light
#define fanpin 33 //fan connector
#define enc  26 //encoder pin for rpm measurement

//Setup of PWM channels
const int freq       = 20000; //PWM frequency: 20 kHz
const int resolution = 8; //PWM with 8 bit (0 to 255)
const int enginePWM  = 0; //PWM channel #0 of the ESP32 (you can have different channels with different frequencies at the same time)
const int frontLED   = 1;
const int rearLED    = 2; 
const int fanPWM     = 3;

//Add peripherals
Adafruit_ADS1115 adc; //define ADC in sketch
#define u_sense  0 //channel 0 of ADS1115; voltage 
#define i_sense  1 //channel 1 of ADS1115; current
#define t0_sense 2 //channel 2 of ADS1115; thermistor 1
#define t1_sense 3 //channel 3 of ADS1115; thermistor 2

Adafruit_PWMServoDriver servo = Adafruit_PWMServoDriver(); //define servo driver; based on the example of the Adafruit PWMServoDriver library
#define SERVOMIN 150 // This is the 'minimum' pulse length count (out of 4096)
#define SERVOMAX 600 // This is the 'maximum' pulse length count (out of 4096)
#define USMIN 600 // This is the rounded 'minimum' microsecond length based on the minimum pulse of 150
#define USMAX 2400 // This is the rounded 'maximum' microsecond length based on the maximum pulse of 600

//Global variables
long volatile counter = 0;
int rpm               = 0;
int mainspeed         = 0;
int speed             = 0;
int mspeed            = 0;
int thedir            = 0;
int rctimer           = 0;
int analogcounter     = 0;
int i_val             = 0;
int u_val             = 0;
int t0_val            = 0;
int t1_val            = 0;
int blinkcounter      = 0;
int signaltimer       = 0;
int threshold         = 1000;
int protocol          = 0;
int channel           = 0;
int counts            = 0;
int loggingtimer      = 0;
bool sendercheck      = false;
int signalquality     = 0;
bool loggingon        = false;
double setpoint       = 0;
double input          = 0;
int error             = 0;
double acs712         = 2.505; //this value sets the zero-current-draw output of the ACS712. It is 2.5 according to the datasheet but may be off a little bit.

void IRAM_ATTR INT0_ISR(){ //interrupt used for tacho sensor
  counter++; //the interrupt is kept as simple as possible to allow a fast execution
}

//ESP-NOW setup
/*
  Rui Santos & Sara Santos - Random Nerd Tutorials
  Complete project details at https://RandomNerdTutorials.com/esp-now-two-way-communication-esp32/
  Permission is hereby granted, free of charge, to any person obtaining a copy of this software and associated documentation files.
  The above copyright notice and this permission notice shall be included in all copies or substantial portions of the Software.
*/

uint8_t FirstMAC[] = {0xBE, 0xA0, 0xBE, 0xEF, 0xFE, 0xED}; //we will set this MAC address for the car
uint8_t SecondMAC[] = {0xB0, 0xAD, 0xBE, 0xEF, 0xFE, 0xED}; //we will set this MAC address for the remote control
uint8_t ThirdMAC[] = {0xBE, 0xAE, 0xBE, 0xEF, 0xFE, 0xED}; //we will set this MAC address for the logging ESP32
uint8_t broadMAC[] = {0xFF, 0xFF, 0xFF, 0xFF, 0xFF, 0xFF}; //using this MAC address as a receiver means broadcasting (no confirmation from receiver)

//Structure to send data; must match the receiver structure of the RC!
typedef struct send_message {
  int voltage;
  int current;
  int temp1;
  int temp2;
  int rpm;
  int signal;
} send_message;

// Create a structured object
send_message outgoing;

//Structure to send data; must match the receiver structure of the data logger!
typedef struct logging_message {
  int rpm;
  int voltage;
  int current;
  int input;
  int motorpwm;
  int elapsedtime;
  int motor;
} logging_message;

logging_message outgoing2;

//Structure to receive data; must match the sender structure of the RC!
typedef struct receive_message {
  int mainspeed;
  int steering;
  int frontlight;
  int rearlight;
  int fan;
  int control;
  int motor;
  int clim;
  int protocol;
  int channel;
} receive_message;

receive_message incoming;

//Structure to send data; must match the receiver structure of the data logger!
typedef struct receive_message2 {
  bool logging;
} receive_message2;

receive_message2 incoming2;

// Callback when data is received
void OnDataRecv(const uint8_t * mac, const uint8_t *incomingData, int len) {
  bool sendercheck = true;
  for (int i = 0; i< 6; i++){ //When using ESP-NOW in broadcast mode, this code snippet ensures that only paired devices communicate with each other (verifying the sender's MAC address)
    if (mac[i] != SecondMAC[i]){
      sendercheck = false;
      break;
    }
  }
  if (sendercheck&&len==40){ //only process the data if it is from the RC and if the packet has the correct length (data from the car to logger has a different length!)
    memcpy(&incoming, incomingData, sizeof(incoming));
    signaltimer = millis();
    if (signalquality<100){
      signalquality = signalquality+1; 
    }        
  } 
   //same procedure when checking if the data logger is present
  sendercheck = true;
  for (int i = 0; i< 6; i++){
    if (mac[i] != ThirdMAC[i]){
      sendercheck = false;
      break;
    }
  }  
  if (sendercheck&&len==1){
    memcpy(&incoming2, incomingData, sizeof(incoming2));
    loggingon = incoming2.logging;      
  } 
}
esp_now_peer_info_t peerInfo; //make sure that the ESP-NOW lines are in the exact same order as in this sketch. Otherwise, there may be malfunctions.

//the preferences library allows you to store variable values within the flash so that their value can be retrieved on startup. Used to store user-adjustable settings.
Preferences preferences; 

void setup() {

  Serial.begin(115200); //Optional - for debugging

  //specify GPIO pin usage
  pinMode(dir, OUTPUT);
  digitalWrite(dir, LOW);
  pinMode(pwm, OUTPUT);
  digitalWrite(pwm, LOW);
  pinMode(front, OUTPUT);
  digitalWrite(front, LOW);
  pinMode(rear, OUTPUT);
  digitalWrite(rear, LOW);
  pinMode(fanpin, OUTPUT);
  digitalWrite(fanpin, LOW);  
  pinMode(enc, INPUT_PULLUP);
  attachInterrupt(digitalPinToInterrupt(enc), INT0_ISR, FALLING);

  preferences.begin("Defaults", false); //Retrieve stored settings from flash memory
  protocol = preferences.getInt("Protocol",0);
  channel  = preferences.getInt("Channel",0);

  //Initialize I2C peripherals
  adc.begin(0x48); //default I2C address of ADS1115 (ADDR pin unconnected/at GND)
  adc.setDataRate(RATE_ADS1115_860SPS); //fastest possible sampling rate for the ADS1115 chip
  servo.begin(); //default I2C address of PCA9685 is 0x40
  servo.setOscillatorFrequency(27000000);
  servo.setPWMFreq(50);  // Analog servos run at ~50 Hz updates
  Wire.setClock(400000); //increase the I2C clock rate from 100 kHz (default) to 400 kHz to increase the data rate

  //this is the setup for the PWM channels
  ledcSetup(enginePWM, freq, resolution); //setup of PWM control: PWM channel, frequency, resolution
  ledcAttachPin(pwm,enginePWM); //Pin attachment: Pin, PWM channel
  ledcWrite(enginePWM, 0); //Pin control: PWM channel, duty cycle

  ledcSetup(frontLED, freq, resolution); //setup of PWM control: PWM channel, frequency, resolution
  ledcAttachPin(front, frontLED); //Pin attachment: Pin, PWM channel
  ledcWrite(frontLED, 0); //Pin control: PWM channel, duty cycle

  ledcSetup(rearLED, freq, resolution); //setup of PWM control: PWM channel, frequency, resolution
  ledcAttachPin(rear, rearLED); //Pin attachment: Pin, PWM channel
  ledcWrite(rearLED, 0); //Pin control: PWM channel, duty cycle

  ledcSetup(fanPWM, freq, resolution); //setup of PWM control: PWM channel, frequency, resolution
  ledcAttachPin(fanpin, fanPWM); //Pin attachment: Pin, PWM channel
  ledcWrite(fanPWM, 0); //Pin control: PWM channel, duty cycle 

  u_val  = readAnalog(u_sense);
  outgoing.voltage = u_val; //voltage is transmitted as the analog readout of the voltage divider (conversion into V is done in the RC)
  i_val  = readAnalog(i_sense);
  outgoing.current = i_val; //current is transmitted as the analog readout of the ACS712 sensor (conversion into A is done in the RC)
  t0_val  = readAnalog(t0_sense);
  outgoing.temp1 = t0_val; //temperature is transmitted as the analog readout of the voltage divider of the NTC thermister (conversion into °C is done in the RC)
  t1_val = readAnalog(t1_sense);
  outgoing.temp2 = t1_val;

  //startup procedure: activate lights and cooling fan for a short time
  ledcWrite(fanPWM, 255);
  for (int i=20; i<=255; i++){
    ledcWrite(frontLED,i);
    ledcWrite(rearLED,i);
    delay(5);
  }
  delay(500);
  ledcWrite(fanPWM, 0);
  for (int i=255; i>=20; i--){
    ledcWrite(frontLED,i);
    ledcWrite(rearLED,i);
    delay(5);
  }
  ledcWrite(frontLED, 0);
  ledcWrite(rearLED, 0);

  // Activate ESP-NOW
  WiFi.mode(WIFI_STA); //Set device as a Wi-Fi Station
  esp_wifi_set_mac(WIFI_IF_STA, FirstMAC); //Overwrite hardware MAC with this new MAC address
  if (protocol==0){
    esp_wifi_set_protocol(WIFI_IF_STA, WIFI_PROTOCOL_11B); //the long range WiFI protocol should theoretically improve the max. distance of the wireless connection (not verified)
  }else if(protocol==1){
    esp_wifi_set_protocol(WIFI_IF_STA, WIFI_PROTOCOL_11B|WIFI_PROTOCOL_11G);
  }else if(protocol==2){
    esp_wifi_set_protocol(WIFI_IF_STA, WIFI_PROTOCOL_11B|WIFI_PROTOCOL_11G|WIFI_PROTOCOL_11N);
  }else if(protocol==3){
    esp_wifi_set_protocol(WIFI_IF_STA, WIFI_PROTOCOL_LR);
  }

  esp_now_init(); // Initialize ESP-NOW

  // Register peer
  memcpy(peerInfo.peer_addr, broadMAC, 6);
  esp_now_add_peer(&peerInfo); // Add peer 

  esp_wifi_set_promiscuous(true); //set WiFi channel
  esp_wifi_set_channel(channel, WIFI_SECOND_CHAN_NONE);
  esp_wifi_set_promiscuous(false);     
  peerInfo.channel = channel;  
  peerInfo.encrypt = false;

  // Register for a callback function that will be called when data is received
  esp_now_register_recv_cb(esp_now_recv_cb_t(OnDataRecv));

  //initialize timers
  rctimer = millis();
  loggingtimer = millis();

}
 
void loop() {

  if (loggingon&&millis()>loggingtimer+10){ //data packages are sent to the data logger every 10 ms - if it has been found as a connected device
    outgoing2.voltage     = u_val;
    outgoing2.current     = i_val;
    outgoing2.input       = mainspeed;
    outgoing2.rpm         = rpm;
    outgoing2.elapsedtime = millis();
    outgoing2.motorpwm    = speed;
    outgoing2.motor       = incoming.motor;
    esp_now_send(broadMAC, (uint8_t *) &outgoing2, sizeof(outgoing2));
    loggingtimer = millis();
  } 

  if (incoming.motor<2&&incoming.clim>0){ //current limit option is available for open-loop PWM and closed-loop speed control
    if (thedir==1&&mainspeed>0){ //it is only active when driving forward
      i_val = readAnalog(i_sense);
      if(i_val>incoming.clim){
        input    = (double(i_val)*0.0001875*(22+33)/33-acs712)/0.066; //conversion of analog values into current in amps
        setpoint = (double(incoming.clim)*0.0001875*(22+33)/33-acs712)/0.066;
        speed    = speed + currentController(setpoint,input); //call the P controller, convert its output with the last value as a sort-of PI controller
        if (speed>255){ //upper and lower boundaries of the controller
          speed = 255;
        }else if (speed<0){
          speed = 0;
        }
        ledcWrite(enginePWM,speed);
      }
    }
  }

  if (incoming.motor>1){ //closed-loop torque controller
    i_val = readAnalog(i_sense); //reading the ADC takes around 2-3 ms; that's the baseline of how often the controller is refreshed
    input = (double(i_val)*0.0001875*(22+33)/33-acs712)/0.066;
    if (input<0){ //the controller is not supposed to deal with negative currents
      input = 0;
    }
    if (mainspeed>=0){ //case: forward driving is requested
      if(thedir==1){
        if (mainspeed>0){
          setpoint = double(mainspeed)*20/255+0.4; //convert input into setpoint: maximum of 20 A; offset by 0.4 A to account for non-motor related power consumption
        }else{
          setpoint = 0.0; //make sure the car doesn't move with the throttle joystick in neutral position due to a current offset in case the actual current draw is lower (e.g., lights off instead of on)
        }
        speed = speed + currentController(setpoint,input);
        if (speed>255){ 
          speed = 255;
        }else if (speed<0){
          speed = 0;
        }
        ledcWrite(enginePWM,speed);
      }else{ //let the car stop if the operator requests forward driving while driving reverse (before calling the torque controller)
        if(speed>0){
          speed = speed-1;
          ledcWrite(enginePWM,speed);
        }else{
          thedir=1;
          digitalWrite(dir, HIGH);         
        }
      }
    }else{ //case: reverse driving is requested (interpolated throttle response, similar to open-loop PWM control)
      if (thedir==0){
        if (abs(mainspeed)>speed){
          speed = speed+1;
          delay(1);
        }else if (abs(mainspeed)<speed){
          speed = speed-1;
          delay(1);
        }
        ledcWrite(enginePWM,speed);
      }else{
        if(speed>0){
          speed = speed-1;
          delay(1);
          ledcWrite(enginePWM,speed);
        }else{
          thedir=0;
          digitalWrite(dir, LOW);
        }        
      }
    }
  }

  if (incoming.steering>149&&incoming.steering<601){//the input for the steering from the RC should always stay in this interval; thus, the servo is only addressed if the value is in this interval
    servo.setPWM(0,0,incoming.steering); //the steering input is processed every loop iteration to prevent any lag
  }

  //the main code within the loop is only executed every 25 ms to let the interrupt measure speed for some ms to reduce noise
  if (millis()>=rctimer+25){ 
    detachInterrupt(digitalPinToInterrupt(enc)); //the interrupt is disabled while running the main loop code
    rpm = counter*120; //conversion of pulse count into rpm: counter*(1000/25)*60/20 [counts times 40 (to get seconds (1000/25), times 60 for minutes, divide by number of slots of encoder wheel (20) for revs/min]
    outgoing.rpm = rpm;

  if (signalquality>0){
    signalquality = signalquality-1; //the RC is supposed to send data packages every 20 ms while the car sends telemetry data every 25-30 ms; thus, the signalquality variable is not reduced by more than 1 when the connection is reliable
  }

  switch (analogcounter){ //only one analog channel is read per loop iteration to reduce the time required per loop run (reading the ADS1115 is comparably slow)
    case 0:
      u_val  = readAnalog(u_sense);
      outgoing.voltage = u_val; 
      analogcounter = 1;
      break;
    case 1:
      i_val  = readAnalog(i_sense);
      outgoing.current = i_val; 
      analogcounter = 2;
      break;
    case 2:  
      t0_val  = readAnalog(t0_sense);
      outgoing.temp1 = t0_val; 
      analogcounter = 3;
      break;
    case 3:  
      t1_val = readAnalog(t1_sense);
      outgoing.temp2 = t1_val;
      analogcounter = 0;
      break;
  }

  mainspeed = incoming.mainspeed; //speed input from the RC is stored in this variable to prevent sudden changes in this value when a new input is received during the loop 

  //change the direction of the main engine according to the input from the RC and the current speed (direction is only changed when the current speed is close to 0)
  if (incoming.motor<2){
    if (mainspeed<0&&speed<10){
      digitalWrite(dir, LOW); //switch high/low in this if-statement if the car drives into the wrong direction or flip the motor wires
      thedir = 0;
    }else if(mainspeed>0&&speed<10){
      digitalWrite(dir, HIGH);
      thedir = 1;
    }
  } 

  if (millis()>signaltimer+threshold){ //set the speed to 0 if the connection is lost (defined as no new data package received for 1 s)
    mainspeed = 0;
    incoming.mainspeed = 0;
  }

  if (incoming.motor==1){ //speed controller
    if(mainspeed>25&&counter>0&&counter<100){ //only apply the speed controller if more than 10% PWM duty cycle is requested (equals approx. 4km/h if no significant rpm drop under load occurs) and when the rpm is within reasonable limits
      updateMotor(speedController(mainspeed,counter));
    }else{
      mspeed = speed; //reset the speed controller whenever it not in use
      error = 0;
      updateMotor(mainspeed);
    }
  }

  if (incoming.motor==0){ //open-loop PWM controller
    updateMotor(mainspeed); 
  }

  if (millis()<signaltimer+threshold){ //fan and light control depend on whether the RC is connected
    if (incoming.frontlight>0){ //the head light, tail light, and fan are PWM-controlled based on the input from the RC
      ledcWrite(frontLED,incoming.frontlight);
    }else{
      ledcWrite(frontLED,0);
    }
    if (incoming.rearlight>0){ 
      ledcWrite(rearLED,incoming.rearlight);
    }else{
      ledcWrite(rearLED,0);
    }  
    if (incoming.fan>0){
      ledcWrite(fanPWM,incoming.fan);
    }else{
      ledcWrite(fanPWM,0);
    }    
  }else{ //the lights blink if the RC is not connected; the fan is off
    ledcWrite(fanPWM,0);
    blinkcounter=blinkcounter+1;
    if (blinkcounter<10){
      ledcWrite(rearLED,100);
      ledcWrite(frontLED,50);
    }else{
      ledcWrite(rearLED,0);
      ledcWrite(frontLED,0);
    }
    if(blinkcounter>19){
      blinkcounter=0;
    }
  }
 
    outgoing.signal = signalquality;
    esp_now_send(broadMAC, (uint8_t *) &outgoing, sizeof(outgoing));  
    preferences.putInt("Protocol",incoming.protocol);
    preferences.putInt("Channel",incoming.channel);

    rctimer = millis();
    counter = 0;
    attachInterrupt(digitalPinToInterrupt(enc), INT0_ISR, FALLING); //the interrupt is enabled again once this code is completed
  } 

}

int currentController(double setpoint, double input){ //P controller for torque
  double value = 0.04*(setpoint - input)*255/20; //maximum change per iteration: 10 out of 255 (PWM duty cycle) -> at least 50 ms to reach max PWM
  if (value>0){
    value = ceil(value);
  }else{
    value = floor(value);
  }
  return value;
}

int speedController(int setpoint, int input){ //PD controller for speed
  input = input*3.27; //get 255 counts for approx. 40 km/h, which is the designated maximum of the speed controller
  double value = 0.06*(setpoint-input)+0.02*((setpoint-input)-error);
  error = setpoint-input; //this is the "last error", from when the function was called last time, for the D term
  mspeed = mspeed+round(value);
  if (mspeed<25){ //set upper and lower limits for the controller
    mspeed=25;
  }else if (mspeed>255){
    mspeed=255;
  }
  return mspeed;
}
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

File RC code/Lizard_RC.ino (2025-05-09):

/*
  This code is developed for Lizard, an open source RC car. This code runs on the remote control's microcontroller.
  The code was designed in Arduino IDE for an ESP32 microcontroller (ESP32-WROOM-32U; 38 pin version of NodeMCU developer board)
*/

/*
  IMPORTANT: This code is written for esp32 boards manager version 2 (tested successfully with esp32 2.0.17).
  It does not work with 3.x.x versions of Espressif Systems' esp32 boards managers (see also https://docs.espressif.com/projects/arduino-esp32/en/latest/migration_guides/2.x_to_3.0.html).
*/

//Required libraries
#include <Wire.h> //library for I2C devices
#include <Adafruit_GFX.h> //library for graphics functions of various displays
#include <Adafruit_SSD1306.h> //library for OLED with SSD1306 driver chip
#include <Adafruit_ADS1X15.h> //library for ADS1115 ADC
#include <WiFi.h> //library for wireless communication
#include <esp_now.h> //library for bidirectional wireless communication between two ESP32
#include <esp_wifi.h> //needed to adjust the MAC address
#include <Preferences.h> //library for storing variables in flash memory

//Pin definitions
#define LED_LR 16
#define LED_UR 17
#define LED_LL 18
#define LED_UL 19
#define BTN_LR 26
#define BTN_LL 25
#define BTN_UR 27
#define BTN_UL 33

//Global variables
double batvolt      = 0;
double voltage      = 0;
double current      = 0;
int potival         = 0;
int mainspeed       = 0;
int mainspeed1      = 0;
int mainspeed2      = 0;
int steering        = 0;
int btnlrdebounce0  = 0;
int btnlrdebounce1  = 0;
int btnlrv          = 1;
int btnurdebounce0  = 0;
int btnurdebounce1  = 0;
int btnurv          = 1;
int btnlldebounce0  = 0;
int btnlldebounce1  = 0;
int btnllv          = 1;
int btnuldebounce0  = 0;
int btnuldebounce1  = 0;
int btnulv          = 1;
int oledtimer        = 0;
int rctimer         = 0;
int lighton         = 0;
int adj             = 0;
int counter         = 0;
int menu            = 0;
int menuval         = 0;
int calval          = 0;
int joylcen         = 0;
int joyll           = 0;
int joylr           = 0;
int joyltol         = 0;
int joyrcen         = 0;
int joyru           = 0;
int joyrd           = 0;
int joyrtol         = 0;
int flightint       = 0;
int rlightint       = 0;
int leftlimit       = 0;
int rightlimit      = 0;
int batcounter      = 0;
int batlow          = 0;
int lcdcounter      = 0;
int control         = 0;
int dispstat        = 0;
int btncounter      = 0;
double v0           = 0;
double v1           = 0;
double v2           = 0;
double v3           = 0;
double v4           = 0;
double vavg         = 0;
double vmax         = 0;
double p            = 0;
double pmax         = 0;
double pavg         = 0;
double energy       = 0;
int energycounter   = 0;
double t1           = 0;
double t2           = 0;
double t            = 0;
int fanmode         = 0;
int fanspeed        = 0;
int overtemp        = 0;
int tempcounter     = 0;
int stalling        = 0;
int stallcounter    = 0;
double totaltimeout = 0;
int timeout         = 0;
int timeout0        = 0;
int timeout1        = 1;
double track        = 0;
double vavgtotal    = 0;
int speedcounter    = 0;
int currentlimit    = 0;
int steeradj        = 0;
int revs            = 0;
int calctimer       = 0;
int voltage_analog  = 0;
int current_analog  = 0;
int temp1_analog    = 0;
int temp2_analog    = 0;
int signaltimer     = 0;
int threshold       = 999;
int protocol        = 0;
int channel         = 0;
int motorcontrol    = 0;
bool sendercheck    = false;
int signalquality   = 0;
int txbatcounter    = 0;
int txbatlow        = 0;
double acs712       = 2.505; //this value sets the zero-current-draw output of the ACS712. It is 2.5 according to the datasheet but may be off a little bit.

//Add I2C peripherals
Adafruit_ADS1115 adc; //ADS1115
int joyr = 0; //these variables indicate the input channel population of the ADC (right and left joystick, poti, battery voltage)
int joyl = 1;
int poti = 2;
int batt = 3;

//2x SSD1306 OLED display
#define SCREEN_WIDTH 128 // OLED display width, in pixels
#define SCREEN_HEIGHT 64 // OLED display height, in pixels
#define OLED_RESET -1 // Reset pin # (or -1 if sharing Arduino reset pin)
#define SCREEN_ADDRESS 0x3D //OLED display 0 (left display)
#define SCREEN_ADDRESS1 0x3C //OLED display 1 (right display)
Adafruit_SSD1306 display(SCREEN_WIDTH, SCREEN_HEIGHT, &Wire, OLED_RESET, 1000000UL, 400000UL); //The last two values set the I2C clock rate. Decrease them in case you encounter stability issues
Adafruit_SSD1306 display1(SCREEN_WIDTH, SCREEN_HEIGHT, &Wire, OLED_RESET, 1000000UL, 400000UL); //The last two values set the I2C clock rate. Decrease them in case you encounter stability issues
int diamond = 0x04; //diamond symbol for the screen

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
e and associated documentation files.
  The above copyright notice and this permission notice shall be included in all copies or substantial portions of the Software.
*/

uint8_t FirstMAC[] = {0xBE, 0xA0, 0xBE, 0xEF, 0xFE, 0xED}; //we will set this MAC address for the car
uint8_t SecondMAC[] = {0xB0, 0xAD, 0xBE, 0xEF, 0xFE, 0xED}; //we will set this MAC address for the remote control
uint8_t ThirdMAC[] = {0xBE, 0xAE, 0xBE, 0xEF, 0xFE, 0xED}; //we will set this MAC address for the logging ESP32
uint8_t broadMAC[] = {0xFF, 0xFF, 0xFF, 0xFF, 0xFF, 0xFF}; //using this MAC address as a receiver for sending packages means broadcasting (ignoring if the data has been received)

// Structure to send data; must match the receiver structure of the car!
typedef struct send_message {
  int mainspeed;
  int steering;
  int frontlight;
  int rearlight;
  int fan;
  int control;
  int motor;
  int clim;
  int protocol;
  int channel;
} send_message;

// Create a structured object
send_message outgoing;

//Structure to receive data; must match the sender structure of the car!
typedef struct receive_message {
  int voltage;
  int current;
  int temp1;
  int temp2;
  int rpm;
  int signal;
} receive_message;

receive_message incoming;

// Callback when data is received
void OnDataRecv(const uint8_t * mac, const uint8_t *incomingData, int len) {
  bool sendercheck = true;
  for (int i = 0; i< 6; i++){ //When using ESP-NOW in broadcast mode, this code snippet ensures that only paired devices communicate with each other (verifying the sender's MAC address)
    if (mac[i] != FirstMAC[i]){
      sendercheck = false;
      break;
    }
  }
  if (sendercheck&&len==24){ //2nd approval step: only process the data if it is from the car and if the packet has the correct length (e.g., data from car to logger has a different length)
    memcpy(&incoming, incomingData, sizeof(incoming)); //write received data into the incoming-structure to make use of them
    signaltimer = millis();  
    if (signalquality<100){ //this snippet helps to check if the car is online: the "signalquality" variable is only counted up if data is received regularly
      signalquality = signalquality+1; 
    }
  }
}
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
